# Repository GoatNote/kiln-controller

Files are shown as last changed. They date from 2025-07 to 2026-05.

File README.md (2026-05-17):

Kiln Controller
==========

Turns a Raspberry Pi into an inexpensive, web-enabled kiln controller.
PCB is configured for MAX31856 board.

## Features

  * supports [many boards](https://github.com/jbruce12000/kiln-controller/blob/main/docs/supported-boards.md) into addition to raspberry pi
  * supports Adafruit MAX31856 thermocouple boards
  * support for K, J, N, R, S, T, E, or B type thermocouples
  * easy to create new kiln schedules and edit / modify existing schedules
  * no limit to runtime - fire for days if you want
  * view status from multiple devices at once - computer, tablet etc
  * real-time firing cost estimate
  * real-time heating rate displayed in degrees per hour
  * supports PID parameters you tune to your kiln
  * monitors temperature in kiln after schedule has ended
  * api for starting and stopping at any point in a schedule
  * accurate simulation
  * support for shifting schedule when kiln cannot heat quickly enough
  * support for skipping first part of profile to match current kiln temperature
  * prevents integral wind-up when temperatures not near the set point
  * automatic restarts if there is a power outage or other event
  * support for a watcher to page you via slack if you kiln is out of whack
  * easy scheduling of future kiln runs

**Run Kiln Schedule**



**Edit Kiln Schedule**



## Hardware

### Parts

| Image | Hardware | Description |
| ---| --- | --- |
|  | [Raspberry Pi](https://www.adafruit.com/category/105) | Virtually any Raspberry Pi will work since only a few GPIO pins are being used. Any board supported by [blinka](https://circuitpython.org/blinka) and has SPI should work. You'll also want to make sure the board has wifi. If you use something other than a Raspberry PI and get it to work, let me know. |
|  | [Adafruit MAX31855](https://www.adafruit.com/product/269) or [Adafruit MAX31856](https://www.adafruit.com/product/3263) | Thermocouple breakout board |
|  | [Thermocouple](https://www.auberins.com/index.php?main_page=product_info&cPath=20_3&products_id=39) | Invest in a heavy duty, ceramic thermocouple designed for kilns. Make sure the type will work with your thermocouple board. Adafruit-MAX31855 works only with K-type. Adafruit-MAX31856 is flexible and works with many types, but folks usually pick S-type. |
|  | Breadboard | breadboard, ribbon cable, connector for pi's gpio pins & connecting wires |
|  | Solid State Relay | Zero crossing, make sure it can handle the max current of your kiln. Even if the kiln is 220V you can buy a single [3 Phase SSR](https://www.auberins.com/index.php?main_page=product_info&cPath=2_30&products_id=331). It's like having 3 SSRs in one.  Relays this big always require a heat sink. |
|  | Electric Kiln | There are many old electric kilns on the market that don't have digital controls. You can pick one up on the used market cheaply.  This controller will work with 110V or 220V (pick a proper SSR). My kiln is a Skutt KS-1018. |

### Schematic

**WARNING** This project involves high voltages and high currents. Please make sure that anything you build conforms to local electrical codes and aligns with industry best practices.

**Note:** The GPIO configuration in this schematic does not match the defaults, check [config](https://github.com/jbruce12000/kiln-controller/blob/main/config.py) and make sure the gpio pin configuration aligns with your actual connections.



## Software 

### Raspberry PI OS

Download [Raspberry PI OS](https://www.raspberrypi.org/software/). Use Rasberry PI Imaging tool to install the OS on an SD card. Boot the OS, open a terminal and...

    $ sudo apt-get update
    $ sudo apt-get dist-upgrade
    $ git clone https://github.com/jbruce12000/kiln-controller
    $ cd kiln-controller
    $ python3 -m venv venv
    $ source venv/bin/activate
    $ pip install -r requirements.txt

*Note: The above steps work on ubuntu if you prefer*

### Raspberry PI deployment

If you're done playing around with simulations and want to deploy the code on a Raspberry PI to control a kiln, you'll need to do this in addition to the stuff listed above:

    $ sudo raspi-config
    interfacing options -> SPI -> Select Yes to enable
    select reboot

## Configuration

All parameters are defined in config.py. You need to read through config.py carefully to understand each setting. Here are some of the most important settings:

| Variable | Default | Description |
| --- | --- | --- |
| sensor_time_wait | 2 seconds | It's the duty cycle for the entire system.  It's set to two seconds by default which means that a decision is made every 2s about whether to turn on relay[s] and for how long. If you use mechanical relays, you may want to increase this. At 2s, my SSR switches 11,000 times in 13 hours. |
| temp_scale | f | f for farenheit, c for celcius |
| pid parameters | | Used to tune your kiln. See PID Tuning. |
| simulate | True | Simulate a kiln. Used to test the software by new users so they can check out the features. |

## Testing

After you've completed connecting all the hardware together, there are scripts to test the thermocouple and to test the output to the solid state relay. Read the scripts below and then start your testing. First, activate the virtual environment like so...

     $ source venv/bin/activate

then test the thermocouple with:

     $ ./test-thermocouple.py

then test the output with:

     $ ./test-output.py

and you can use this script to examine each pin's state including input/output/voltage on your board:

     $ ./gpioreadall.py

## PID Tuning

Run the [autotuner](https://github.com/jbruce12000/kiln-controller/blob/main/docs/ziegler_tuning.md). It will heat your kiln to 400F, pass that, and then once it cools back down to 400F, it will calculate PID values which you must copy into config.py. No tuning is perfect across a wide temperature range. Here is a [PID Tuning Guide](https://github.com/jbruce12000/kiln-controller/blob/main/docs/pid_tuning.md) if you end up having to manually tune.

There is a state view that can help with tuning. It shows the P,I, and D parameters over time plus allows for a csv dump of data collected. It also shows lots of other details that might help with troubleshooting issues. Go to /state.

## Usage

### Server Startup

    $ source venv/bin/activate; ./kiln-controller.py

### Autostart Server onBoot
If you want the server to autostart on boot, run the following command:

    $ /home/pi/kiln-controller/start-on-boot

### Client Access

Click http://127.0.0.1:8081 for local development or the IP
of your PI and the port defined in config.py (default 8081).

### Simulation

In config.py, set **simulate=True**. Start the server and select a profile and click Start. Simulations run at near real time.

### Scheduling a Kiln run

If you want to schedule a kiln run to start in the future. Here are [examples](https://github.com/jbruce12000/kiln-controller/blob/main/docs/scheduling.md).

### Watcher

If you're busy and do not want to sit around watching the web interface for problems, there is a watcher.py script which you can run on any machine in your local network or even on the raspberry pi which will watch the kiln-controller process to make sure it is running a schedule, and staying within a pre-defined temperature range. When things go bad, it sends messages to a slack channel you define. I have alerts set on my android phone for that specific slack channel. Here are detailed [instructions](https://github.com/jbruce12000/kiln-controller/blob/main/docs/watcher.md).

## License

This program is free software: you can redistribute it and/or modify
it under the terms of the GNU General Public License as published by
the Free Software Foundation, either version 3 of the License, or
(at your option) any later version.

This program is distributed in the hope that it will be useful,
but WITHOUT ANY WARRANTY; without even the implied warranty of
MERCHANTABILITY or FITNESS FOR A PARTICULAR PURPOSE.  See the
GNU General Public License for more details.

You should have received a copy of the GNU General Public License
along with this program.  If not, see <http://www.gnu.org/licenses/>.

## Support & Contact

Please use the issue tracker for project related issues.
If you're having trouble with hardware, I did too.  Here is a [troubleshooting guide](https://github.com/jbruce12000/kiln-controller/blob/main/docs/troubleshooting.md) I created for testing RPi gpio pins.

## Origin
This project was originally forked from https://github.com/apollo-ng/picoReflow but has diverged a large amount.

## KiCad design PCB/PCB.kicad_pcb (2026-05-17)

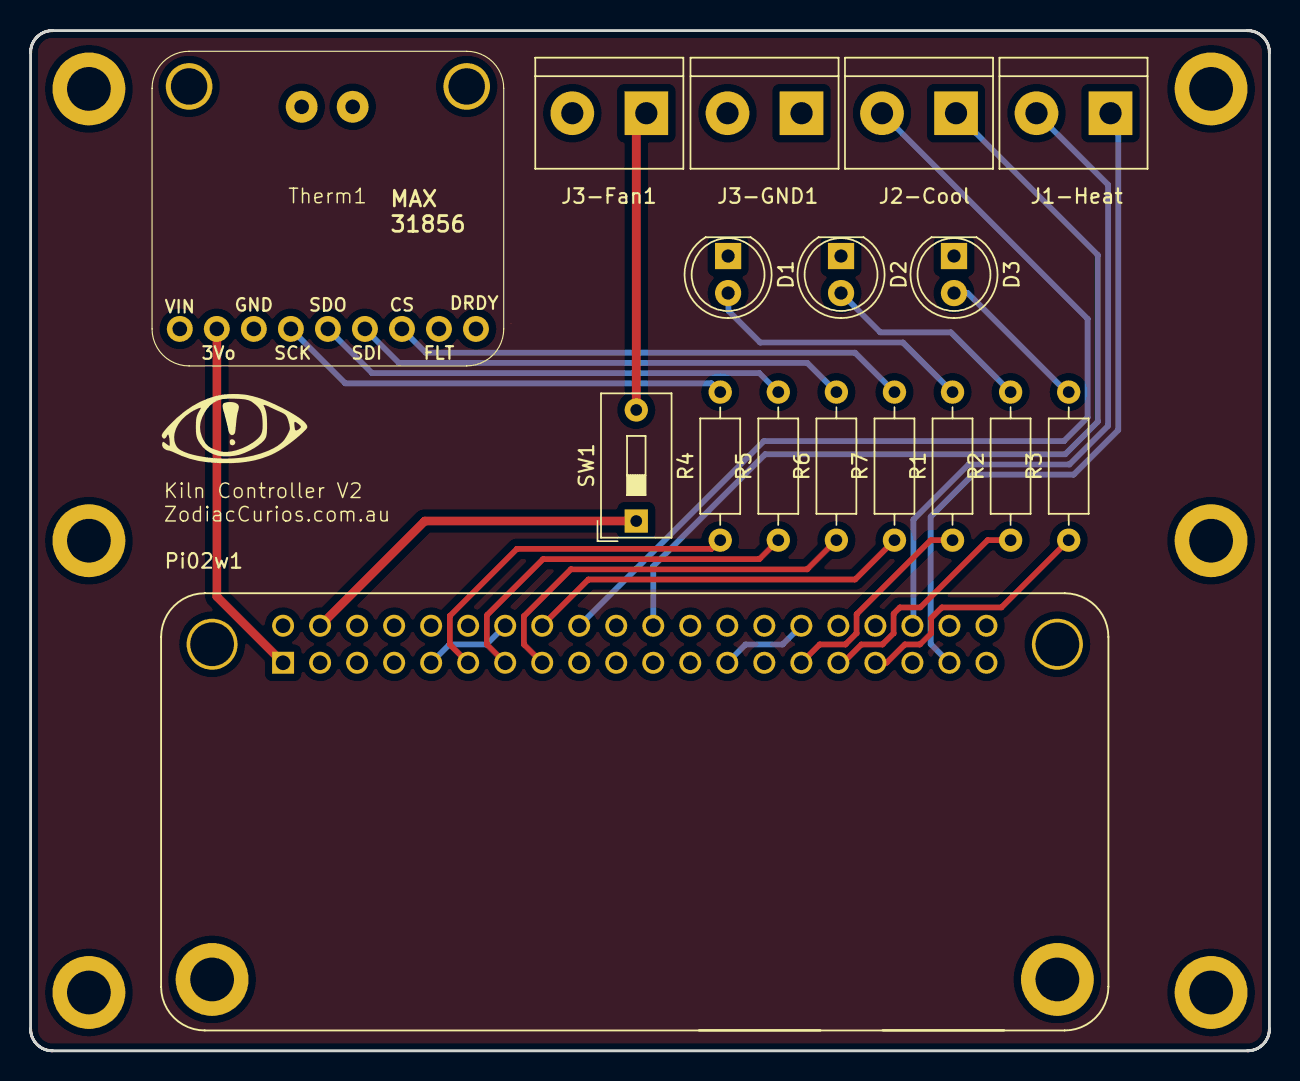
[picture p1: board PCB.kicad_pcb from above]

Board: 2 copper layers, 85.0 x 70.0 mm, 17 parts (0 on the bottom side), 22 nets.

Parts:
D1, D2, D3: LED; LED_D5.0mm
J1-Heat, J2-Cool, J3-Fan1, J3-GND1: Screw_Terminal_01x02; TerminalBlock_bornier-2_P5.08mm
Pi02w1: SC1176; MODULE_SC1176
R1, R2, R3, R4, R5, R6, R7: R; R_Axial_DIN0207_L6.3mm_D2.5mm_P10.16mm_Horizontal
SW1: SW_SPST; SW_DIP_SPSTx01_Slide_9.78x4.72mm_W7.62mm_P2.54mm
Therm1: MAX31856

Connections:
GND: D1.1 (K), D2.1 (K), D3.1 (K), J3-Fan1.2, J3-GND1.1, J3-GND1.2, Pi02w1.6 (GND_6), Pi02w1.9 (GND_9), Pi02w1.14 (GND_14), Pi02w1.20 (GND_20), Pi02w1.25 (GND_25), Pi02w1.30 (GND_30), Pi02w1.34 (GND_34), Pi02w1.39 (GND_39), Therm1.7
unnamed: D1.2 (A), R1.2
unnamed: D2.2 (A), R2.2
unnamed: D3.2 (A), R3.2
unnamed: J1-Heat.1, Pi02w1.37 (GPIO26)
unnamed: J1-Heat.2, Pi02w1.36 (GPIO16)
unnamed: J2-Cool.1, Pi02w1.22 (GPIO25/GPIO_GEN6)
unnamed: J2-Cool.2, Pi02w1.18 (GPIO24/GPIO_GEN5)
unnamed: J3-Fan1.1, SW1.2 (B)
unnamed: Pi02w1.1 (3V3_1), Therm1.8
unnamed: Pi02w1.4 (5V_4), SW1.1 (A)
unnamed: Pi02w1.29 (GPIO5), R1.1
unnamed: Pi02w1.31 (GPIO6), R2.1
unnamed: Pi02w1.33 (GPIO13), R3.1
unnamed: Pi02w1.11 (GPIO17/GPIO_GEN0), R4.1
unnamed: Pi02w1.15 (GPIO22/GPIO_GEN3), R6.1
unnamed: Pi02w1.16 (GPIO23/GPIO_GEN4), R7.1
unnamed: Pi02w1.13 (GPIO27/GPIO_GEN2), R5.1
unnamed: R4.2, Therm1.6
unnamed: R5.2, Therm1.5
unnamed: R6.2, Therm1.4
unnamed: R7.2, Therm1.3

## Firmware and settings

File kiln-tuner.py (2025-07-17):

#!/usr/bin/env python

import os
import sys
import csv
import time
import argparse

try:
        sys.dont_write_bytecode = True
        import config
        sys.dont_write_bytecode = False

except ImportError:
        print("Could not import config file.")
        print("Copy config.py.EXAMPLE to config.py and adapt it for your setup.")
        exit(1)


def recordprofile(csvfile, targettemp):

    script_dir = os.path.dirname(os.path.realpath(__file__))
    sys.path.insert(0, script_dir + '/lib/')

    from oven import RealOven, SimulatedOven

    # open the file to log data to
    f = open(csvfile, 'w')
    csvout = csv.writer(f)
    csvout.writerow(['time', 'temperature'])

    # construct the oven
    if config.simulate:
        oven = SimulatedOven()
        oven.target = targettemp * 2 # insures max heating for simulation
    else:
        oven = RealOven()

    # Main loop:
    #
    # * heat the oven to the target temperature at maximum burn.
    # * when we reach it turn the heating off completely.
    # * wait for it to decay back to the target again.
    # * quit
    #
    # We record the temperature every config.sensor_time_wait
    try:

        # heating to target of 400F
        temp = 0
        sleepfor = config.sensor_time_wait
        stage = "heating"
        while(temp <= targettemp):
            if config.simulate:
                oven.heat_then_cool()
            else:
                oven.output.heat(sleepfor)
            temp = oven.board.temp_sensor.temperature() + \
                config.thermocouple_offset
            
            print("stage = %s, actual = %.2f, target = %.2f" % (stage,temp,targettemp))
            csvout.writerow([time.time(), temp])
            f.flush()

        # overshoot past target of 400F and then cooling down to 400F
        stage = "cooling"
        if config.simulate:
            oven.target = 0
        while(temp >= targettemp):
            if config.simulate:
                oven.heat_then_cool()
            else:
                oven.output.cool(sleepfor)
            temp = oven.board.temp_sensor.temperature() + \
                config.thermocouple_offset
            
            print("stage = %s, actual = %.2f, target = %.2f" % (stage,temp,targettemp))
            csvout.writerow([time.time(), temp])
            f.flush()

    finally:
        f.close()
        # ensure we always shut the oven down!
        if not config.simulate:
            oven.output.cool(0)


def line(a, b, x):
    return a * x + b


def invline(a, b, y):
    return (y - b) / a


def plot(xdata, ydata,
         tangent_min, tangent_max, tangent_slope, tangent_offset,
         lower_crossing_x, upper_crossing_x):
    from matplotlib import pyplot

    minx = min(xdata)
    maxx = max(xdata)
    miny = min(ydata)
    maxy = max(ydata)

    pyplot.scatter(xdata, ydata)

    pyplot.plot([minx, maxx], [miny, miny], '--', color='purple')
    pyplot.plot([minx, maxx], [maxy, maxy], '--', color='purple')

    pyplot.plot(tangent_min[0], tangent_min[1], 'v', color='red')
    pyplot.plot(tangent_max[0], tangent_max[1], 'v', color='red')
    pyplot.plot([minx, maxx], [line(tangent_slope, tangent_offset, minx), line(tangent_slope, tangent_offset, maxx)], '--', color='red')

    pyplot.plot([lower_crossing_x, lower_crossing_x], [miny, maxy], '--', color='black')
    pyplot.plot([upper_crossing_x, upper_crossing_x], [miny, maxy], '--', color='black')

    pyplot.show()


def calculate(filename, tangentdivisor, showplot):
    # parse the csv file
    xdata = []
    ydata = []
    filemintime = None
    with open(filename) as f:
        for row in csv.DictReader(f):
            try:
                time = float(row['time'])
                temp = float(row['temperature'])
                if filemintime is None:
                    filemintime = time

                xdata.append(time - filemintime)
                ydata.append(temp)
            except ValueError:
                continue  # just ignore bad values!

    # gather points for tangent line
    miny = min(ydata)
    maxy = max(ydata)
    midy = (maxy + miny) / 2
    yoffset = int((maxy - miny) / tangentdivisor)
    tangent_min = tangent_max = None
    for i in range(0, len(xdata)):
        rowx = xdata[i]
        rowy = ydata[i]

        if rowy >= (midy - yoffset) and tangent_min is None:
            tangent_min = (rowx, rowy)
        elif rowy >= (midy + yoffset) and tangent_max is None:
            tangent_max = (rowx, rowy)

    # calculate tangent line to the main temperature curve
    tangent_slope = (tangent_max[1] - tangent_min[1]) / (tangent_max[0] - tangent_min[0])
    tangent_offset = tangent_min[1] - line(tangent_slope, 0, tangent_min[0])

    # determine the point at which the tangent line crosses the min/max temperaturess
    lower_crossing_x = invline(tangent_slope, tangent_offset, miny)
    upper_crossing_x = invline(tangent_slope, tangent_offset, maxy)

    # compute parameters
    L = lower_crossing_x - min(xdata)
    T = upper_crossing_x - lower_crossing_x

    # Magic Ziegler-Nicols constants ahead!
    Kp = 1.2 * (T / L)
    Ti = 2 * L
    Td = 0.5 * L
    Ki = Kp / Ti
    Kd = Kp * Td

    # output to the user
    print("pid_kp = %s" % (Kp))
    print("pid_ki = %s" % (1 / Ki))
    print("pid_kd = %s" % (Kd))

    config.pid_kp=Kp
    config.pid_ki=(1/Ki)
    config.pid_kd=Kd
    print("Code has input PID values into config file.")

    if showplot:
        plot(xdata, ydata,
             tangent_min, tangent_max, tangent_slope, tangent_offset,
             lower_crossing_x, upper_crossing_x)


if __name__ == "__main__":
    parser = argparse.ArgumentParser(description='Kiln tuner')
    parser.add_argument('-c', '--calculate_only', action='store_true')
    parser.add_argument('-t', '--target_temp', type=float, default=400, help="Target temperature")
    parser.add_argument('-d', '--tangent_divisor', type=float, default=8, help="Adjust the tangent calculation to fit better. Must be >= 2 (default 8).")
    parser.add_argument('-s', '--showplot', action='store_true', help="draw plot so you can see tanget line and possibly change")
    args = parser.parse_args()

    csvfile = "tuning.csv"
    target = args.target_temp
    if config.temp_scale.lower() == "c":
        target = (target - 32)*5/9
    tangentdivisor = args.tangent_divisor 

    # default behavior is to record profile to csv file tuning.csv
    # and then calculate pid values and print them
    if args.calculate_only:
        calculate(csvfile, tangentdivisor, args.showplot)
    else:
        recordprofile(csvfile, target)
        calculate(csvfile, tangentdivisor, args.showplot)

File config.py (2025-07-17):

import logging
import os
from digitalio import DigitalInOut
import busio

########################################################################
#
#   General options

### Logging
log_level = logging.INFO
log_format = '%(asctime)s %(levelname)s %(name)s: %(message)s'

### Server
listening_port = 8081

########################################################################
# Cost Information
#
# This is used to calculate a cost estimate before a run. It's also used
# to produce the actual cost during a run. My kiln has three
# elements that when my switches are set to high, consume 9460 watts.
kwh_rate        = 0.1319  # cost per kilowatt hour per currency_type to calculate cost to run job
kw_elements     = 9.460 # if the kiln elements are on, the wattage in kilowatts
currency_type   = "$"   # Currency Symbol to show when calculating cost to run job

########################################################################
#
# Hardware Setup (uses BCM Pin Numbering)
#
# kiln-controller.py uses SPI interface from the blinka library to read
# temperature data from the adafruit-31855 or adafruit-31856.
# Blinka supports many different boards. I've only tested raspberry pi.
#
# First you must decide whether to use hardware spi or software spi.
# 
# Hardware SPI
#
# - faster
# - requires 3 specific GPIO pins be used on rpis
# - no pins are listed in this config file 
# 
# Software SPI
#
# - slower (which will not matter for reading a thermocouple
# - can use any GPIO pins
# - pins must be specified in this config file

#######################################
# SPI pins if you choose Hardware SPI #
#######################################
# On the raspberry pi, you MUST use predefined
# pins for HW SPI. In the case of the adafruit-31855, only 3 pins are used:
#
#    SPI0_SCLK = BCM pin 11 = CLK on the adafruit-31855
#    SPI0_MOSI = BCM pin 10 = not connected
#    SPI0_MISO = BCM pin 9  = D0 on the adafruit-31855
#   
# plus a GPIO output to connect to CS. You can use any GPIO pin you want.
# I chose gpio pin 5:
#
#    GPIO5    = BCM pin 5   = CS on the adafruit-31855
#
# Note that NO pins are configured in this file for hardware spi

#######################################
# SPI pins if you choose software spi #
#######################################
# For software SPI, you can choose any GPIO pins you like.
# You must connect clock, mosi, miso and cs each to a GPIO pin
# and configure them below based on your connections.

#######################################
# SPI is Autoconfigured !!!
#######################################
# whether you choose HW or SW spi, it is autodetected. If you list the PINs
# below, software spi is assumed.

#######################################
# Output to control the relay
#######################################
# A single GPIO pin is used to control a relay which controls the kiln.
# I use GPIO pin 23.

try:
    import board
    spi_sclk  = board.D17    #spi clock
    spi_miso  = board.D27    #spi Microcomputer In Serial Out
    spi_cs    = board.D10    #spi Chip Select
    spi_mosi  = board.D22    #spi Microcomputer Out Serial In (not connected) 
    gpio_heat = board.D26    #output that controls relay
    gpio_heat_invert = False #invert the output state
    gpio_status_led1 = board.D5 #status LED GPIO pin1
    gpio_status_led2 = board.D6 #status LED GPIO pin2
    gpio_status_led3 = board.D13 #status LED GPIO pin3
    gpio_door_status = board.D16
except (NotImplementedError,AttributeError):
    print("not running on blinka recognized board, probably a simulation")

#######################################
### Thermocouple breakout boards
#######################################
# There are only two breakoutboards supported. 
#   max31855 - only supports type K thermocouples
#   max31856 - supports many thermocouples
max31855 = 0
max31856 = 1
# uncomment these two lines if using MAX-31856
import adafruit_max31856
thermocouple_type = adafruit_max31856.ThermocoupleType.K

# here are the possible max-31856 thermocouple types
#   ThermocoupleType.B
#   ThermocoupleType.E
#   ThermocoupleType.J
#   ThermocoupleType.K
#   ThermocoupleType.N
#   ThermocoupleType.R
#   ThermocoupleType.S
#   ThermocoupleType.T

########################################################################
#
# If your kiln is above the starting temperature of the schedule when you 
# click the Start button... skip ahead and begin at the first point in 
# the schedule matching the current kiln temperature.
seek_start = True

########################################################################
#
# duty cycle of the entire system in seconds
# 
# Every N seconds a decision is made about switching the relay[s] 
# on & off and for how long. The thermocouple is read 
# temperature_average_samples times during and the average value is used.
sensor_time_wait = 2
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
